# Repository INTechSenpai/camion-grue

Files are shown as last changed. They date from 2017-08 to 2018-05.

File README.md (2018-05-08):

# Après le [moon rover](https://intechsenpai.github.io/moon-rover/), INTech Senpaï est fier de vous présenter son camion grue !

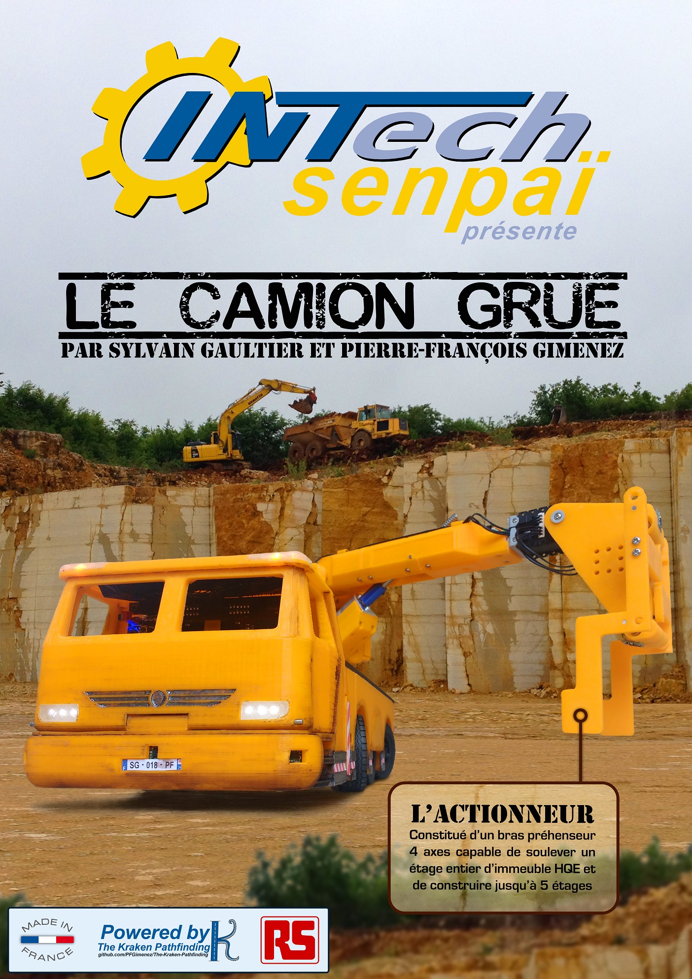
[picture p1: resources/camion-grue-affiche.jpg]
Affiche robot


## INTech Senpaï

INTech Senpaï participe pour la troisième fois à la Coupe de France de Robotique. Après le succès du robot sumo et du moon rover, qui a fini 29e à la coupe 2017, nous revenons en force avec le camion grue.

## Un modèle réduit unique

Notre camion grue est un modèle réduit à l'échelle 1:16 des immenses engins qui ont bercé notre enfance. À taille réelle, il mesurerait 3×7m ! Son design avec ses six roues (dont quatre directrices et motrices), ses feux de recul, de stop, de nuit, ses clignotants, ses gyrophare, sa grue est unique : il a été entièrement conçu par notre équipe.

## Un engin de chantier autonome

Notre camion grue utilise le système Kraken de déplacement autonome, fruit de plus de trois ans de R&D d'un doctorant en intelligence artificielle. Contrairement aux voitures autonomes qui suivent simplement une route, les engins de chantier évoluent dans un environnement encombré et changeant ; trouver un chemin implique un grand nombre de manœuvres qui peuvent être difficiles à trouver, même pour un humain. C'est ce que réalise le système Kraken, qui permet au camion grue de se déplacer avec aisance sur la table de jeu qui représente assez bien ce type d'environnement.

Le système Kraken est un logiciel libre et en [libre accès](https://github.com/PFGimenez/The-Kraken-Pathfinding).

## Un concurrent à la Coupe de France

Enfin, le camion grue est également un compétiteur de la Coupe. Sa grue terminée par une pince lui permet de manipuler des cubes et de les empiler.

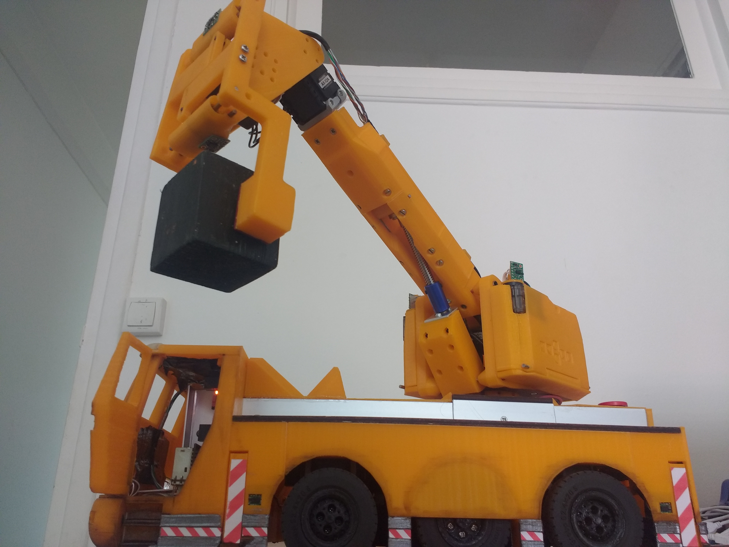
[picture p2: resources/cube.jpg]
Prise d'un cube


## Hardware

Le camion grue est équipé de quatre unités de calcul : trois Teensy pour le contrôle bas niveau et une Raspberry Pi 3+ pour Kraken. Avec ses treize capteurs _time of flight_ dont deux rotatifs, il voit tout son environnement.

On peut voir très bien un capteur _time of flight_ au centre de l'image suivante :

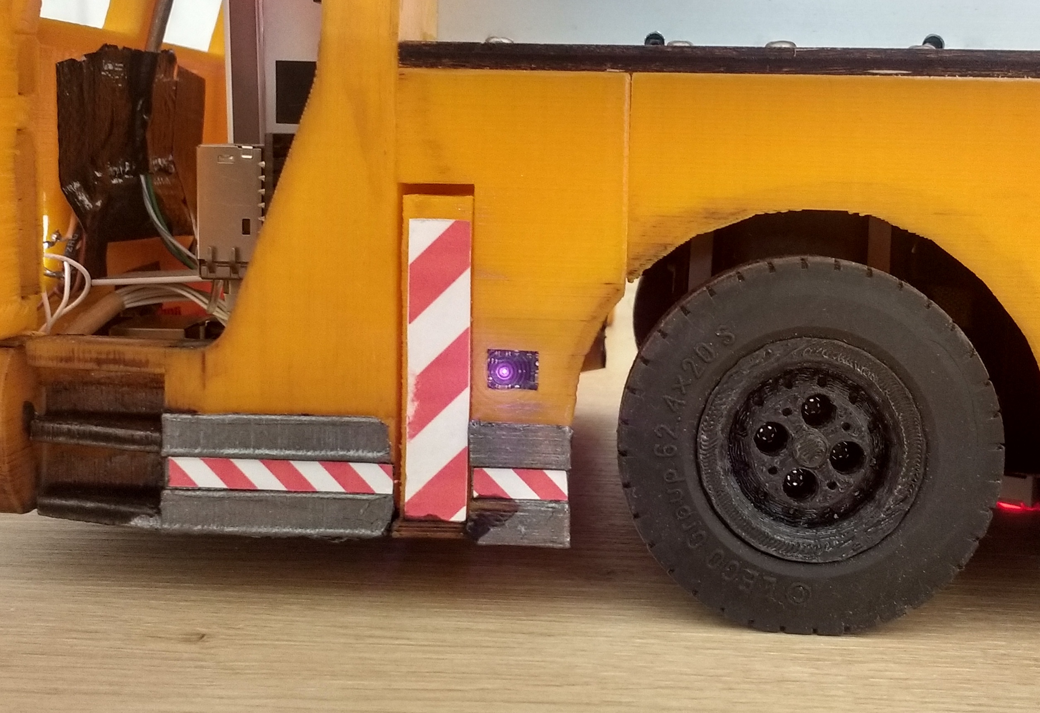
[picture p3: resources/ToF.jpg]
Capteurs ToF


Le camion grue peut facilement être ouvert afin d'accéder à son électronique.

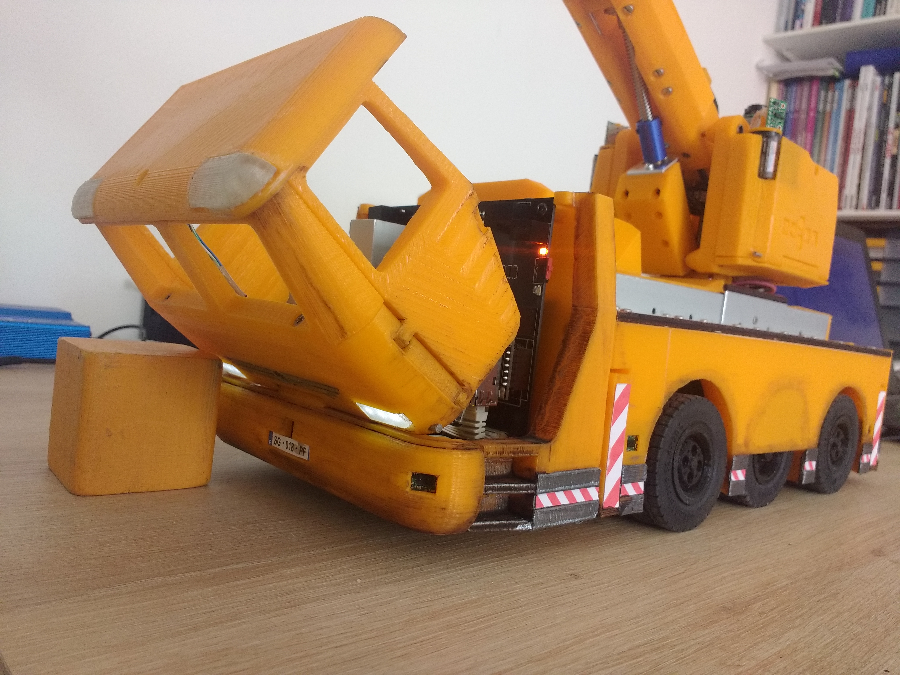
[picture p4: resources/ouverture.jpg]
Mécanisme d'ouverture


Voici une partie de l'électronique du camion. On y voit les radiateurs des ponts en H (au centre), ainsi que deux Teensy (en bas à gauche) et la Raspberry Pi (en bas). L'autre partie de l'électronique se trouve dans la grue.

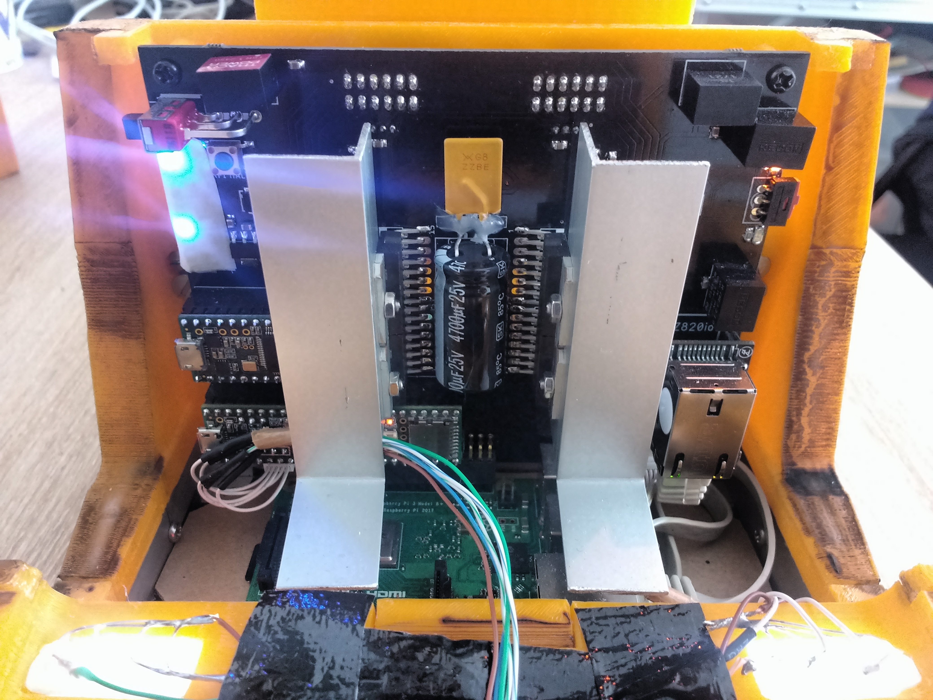
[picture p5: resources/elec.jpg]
Électronique


## L'équipe

[Sylvain Gaultier](https://github.com/sylvaing19) est le fondateur d'INTech Senpaï, il s'occupe de la conception et de la réalisation de la mécanique et de l'électronique du camion grue. Il a également programmé les trois Teensy.

[Pierre-François Gimenez](https://github.com/PFGimenez), doctorant en intelligence artificielle, a été recruté par Sylvain pour son projet de développement d'un camion grue autonome. Il est le concepteur et le programmeur du système Kraken.

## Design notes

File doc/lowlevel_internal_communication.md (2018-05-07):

# Low level: internal communication protocol

## Frame structure

| Header | Instruction | Length |  Payload  | Checksum |
|---|---|---|---|---|
| 0xFFFF | uint8_t | uint8_t| uint8_t[] |  uint8_t |
0        2             3        4          5+N        6+N    Bytes

* Length: number of bytes in the payload

## Instruction set and associated payloads

### [0x00] Sensors board report
uint8_t[9] = [front, front_left, front_right, side_front_left, side_front_right, side_back_left, side_back_right, back_left, back_right]
Values:
[4, MAX_INT]: Distance to the obstacle (mm)
3: No obstacle in front of the sensor
2: obstacle too close to measure (you can consider the distance being the minimum applicable, but not use it for repositionning)
1: Value was not updated yet (use last value instead)
0: Sensor is not working

### [0x01] Set LED lightning mode
uint8_t[1]
Values:
value & b00000001: left_turn_signal
value & b00000010: right_turn_signal
value & b00000100: flashing_lights
value & b00001000: stop_light
value & b00010000: reverse_light
value & b00100000: night_lights_low
value & b01000000: night_lights_high
value & b10000000: alarm_signal

### [0x02] Actuators board move ACK
uint8_t[0]
Indique que "isMoving" vient de passer à "true"

### [0x03] Actuators board report
uint8_t[38]
(bool)moving
(int)status
(bool)cube_in_plier
(int)tof_g
(int)tof_d
(float)angle_t_g
(float)angle_t_d
(float)angle_h_grue
(float)angle_v_grue
(float)angle_head_grue_local
(float)pos_pince_grue

### [0x04] Go to home position
uint8_t[4]
(float) deploy side (-1; 0; +1)
Retour à la position initiale du bras (avec pince entre-ouverte)

### [0x05] Take cube using sensor
uint8_t[4]
(float) angle (h) de prise (approx)

### [0x06] Take cube at fixed position
uint8_t[4]
(float) angle (h) de prise (exact)

### [0x07] Store cube inside robot
uint8_t[0]

### [0x08] Store cube on top
uint8_t[4]
(float) deploy side (-1; 0; +1)

### [0x09] Take cube from storage
uint8_t[4]
(float) deploy side (-1; 0; +1)

### [0x0A] Put cube on pile using sensor 
uint8_t[8]
(float) angle (h) de dépose (approx)
(int)floor (0=sur le sol; étage max: 4)

### [0x0B] Put cube on pile at fixed position
uint8_t[8]
(float) angle (h) de dépose (exact)
(int)floor (0=sur le sol; étage max: 4)

### [0x0C] Put arm at given position
uint8_t[16]
(float)angle_h_grue
(float)angle_v_grue
(float)angle_head_grue_local
(float)pos_pince_grue

### [0x0D] Set sensors angles
uint8_t[8]
(float)angle_t_g
(float)angle_t_d

### [0x0E] Set displayed score
uint8_t[4]
(int)score

### [0x0F] Stop arm
uint8_t[0]

### [0x10] Push button
uint8_t[8]
(float)angleV
(int) deploy side (-1; 0; +1)

### [0x11] Push bee
uint8_t[4]
(float)angleH

### [0x12] Take cube from human
uint8_t[4]
(float) deploy side (-1; 0; +1)

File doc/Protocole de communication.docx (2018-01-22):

# Protocole de communication du microcontrôleur – Eurobotruck 2018

# 1. Généralités

La communication avec le microcontrôleur responsable du contrôle du robot se fait par l’intermédiaire d’une liaison Ethernet sur laquelle est utilisé le protocole TCP/IP.

Le microcontrôleur agit comme un serveur, il peut accepter jusqu’à 4 connexions simultanées.

Un serveur identique, utilisant le même protocole et permettant d’effectuer les mêmes actions écoute également sur le port série RS232 du microcontrôleur. Aucun mécanisme de contrôle d’intégrité de l’information, de correction d’erreurs, ni d’acquittement n’est mis en place dans le protocole que nous définissons ici. La liaison série étant un support n’offrant aucune garantie de ce type, cette dernière présente un moins bon niveau de fiabilité et n’est à utiliser que si la liaison Ethernet est défaillante.

# 2. La trame

La communication entre le client et le serveur est asynchrone et se compose d’une succession de trames, formatées comme suit :

0xFF | ID | Length | Data 0 | … | Data n

Une case = un octet

0xFF : identificateur de début de trame. Simplement un octet contenant la valeur 0xFF.

ID [0x00 – 0xFF] : identifiant de trame. Octet indiquant quelle commande doit être effectuée par le microcontrôleur, ou à l’inverse quelle commande vient d’être effectuée par le microcontrôleur.

Length [0x00 – 0xFE] : taille du champ Data, en nombre d’octets. La taille totale de la trame vaut donc Length + 3. Le champ Data peut contenir, au maximum, 254 octets.

Data : ensemble d’octets contenants les informations nécessaires à l’exécution de la commande. La signification de ces octets est spécifiée plus loin, pour chaque commande.

Cas particulier : la trame d’information

La trame d’information est une trame contenant une chaine de caractères destinée à être lue par un opérateur humain. Elle sera ignorée par le serveur si il en reçois une. Elle suit le même schéma que la trame normale, à deux détails près : Length vaut 0xFF (255) et il n’y a pas de limite de taille pour la trame (la fin de la trame est donnée par le caractère de fin de chaine).

0xFF | ID | 0xFF | Char 0 | … | Char n | End of string

ID [0x00 – 0x1F] : il correspond nécessairement à celui d’un canal de données, et jamais à celui d’un ordre (voir chapitre suivant pour la définition de ces notions).

Char : succession de caractères ASCII destinés à être affichés, il s’agit du code ASCII NON étendu, ce qui interdit l’usage de caractères accentués.

Les caractères autorisés sont : \0 \t \n \r (space) ! “ # $ % & ‘ ( ) * + , - . / 0123456789 : ; < = > ? @ ABCDEFGHIJKLMNOPQRSTUVWXYZ [ \ ] ^ _ ` abcdefghijklmnopqrstuvwxyz { | } ~

Les valeurs décimales correspondantes sont : 0 ; 9 ; 10 ; 13 ; 32–126

End of string [0x00] : caractère ASCII « fin de chaine ». Octet valant zéro.

# 3. Les commandes

L’espace des 256 commandes adressables est divisé en 3 parties :

Plage d’ID | Catégorie
0 – 31 | Inscription aux canaux de données
32 – 127 | Ordres à exécution longue
128 – 255 | Ordres immédiats

## 3.1. Inscription aux canaux de données

Les ordres permettent à un client de spécifier au serveur qu’il souhaite, ou non, recevoir par la suite les informations concernant un certain canal de données. Si le client souscrit à un canal de données, il recevra des trames ayant pour ID le numéro du canal de données et contenant des informations donc le format est spécifié plus bas.

Structure de la trame d’inscription/désinscription :

0xFF | ID du canal | 0x01 | Inscription

ID du canal : valeur entre 0x00 (0) et 0x1F (31) désignant l’un des canaux de données (listés plus loin).

Inscription : 0x00 pour se désinscrire. 0x01 pour s’inscrire.

Aucune réponse ne sera envoyée par le serveur à la suite de cette commande.

Liste des canaux

Identifiant | Désignation | Format des données envoyées sur ce canal
0x00 | ODO_AND_SENSORS | (à déterminer)
0x01
0x02
0x03
0x04
0x05
0x06
…
0x1F

## 3.2. Ordres à exécution longue

On regroupe ici toutes les commandes dont la réalisation nécessite un temps « long », ce qui correspond, en pratique, à tout ce qui nécessite plus d’une milliseconde. On y trouve donc notamment les commandes mettant en œuvre des composants mécaniques.

L’exécution de l’ordre long commence à la réception de la trame de commande et se termine au bout d’un temps à priori inconnu. Une trame sera envoyée par le serveur à la fin de l’exécution de l’ordre long afin d’en notifier le client. Cette trame utilise l’identifiant de la commande et peut contenir, au besoin, des informations relatives à la qualité d’exécution de la commande. Il est interdit d’exécuter un ordre long si un autre ordre long utilisant le même identifiant (i.e. : le même ordre) est encore en cours d’exécution.

Liste des ordres longs

Identifiant | Description | Format des données de la commande | Format de données de la réponse
0x20 | FOLLOW_TRAJECTORY | None | [ARRIVED:0x00, EXT_BLOCKED:0x01, INT_BLOCKED:0x02, NO_MORE_POINTS:0x03, STOP_REQUIRED:0x04, FAR_AWAY:0x05]END_MOVE_STATUS(8) TRAJECTORY_INDEX(8)
0x21 | STOP | None | None
0x22 | WAIT_FOR_JUMPER | None | None
0x23 | START_MATCH_CHRONO
0x24 | RUN_FOR_REMOTE | None | None
0x25
0x26
…
0x7F

## 3.3. Ordres immédiats

On regroupe ici les commandes pouvant être exécutées en un temps très court devant les temps de transmission, typiquement toujours inférieur à une milliseconde. On y trouve principalement des commandes permettant de lire ou de modifier des variables d’état du système.

L’exécution d’un ordre immédiat se fait dès la réception de la trame associée, et peut faire, ou non, l’objet d’une réponse à l’aide d’une trame portant le même identifiant.

Liste des ordres immédiats

Identifiant | Description | Format des données de la commande | Format des données de la réponse
0x80 | PING | None | 0x00 (8)
0x81 | GET_COLOR | None | [ORANGE 0x00, VERT 0x01, INCONNU 0x02] (8)
0x82 | EDIT_POSITION | XYO(40) | None
0x83 | SET_POSITION | XYO(40) | None
0x84 | ADD_TRAJECTORY_POINTS | (À déterminer) | None
0x85 | SET_CURVATURE_FOR_REMOVE | CURVATURE(16) | None
0x86 | SET_SPEED_FOR_REMOTE | SIGNED_SPEED(16) | None
…
0xFF

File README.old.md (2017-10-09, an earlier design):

# Eurobotruck

Eurobotruck est le successeur du moon-rover.

TODO list :

## HL

- améliorer Kraken (objectif : 500 ms max)
- outils de debug
- tourelles
- préparer des démos à l'avance
- autocomplétion de tests + zsh + boot rapide sur linux
- outil de debug de trajectoire courbe (créer facilement des trajectoires)
- télécommande HL

## LL

- outils de debug
- tourelles
- communication par socket TCP/IP (serveur)

## Hardware

- tourelles de visée ToF longue portée (HL donne la position, LL gère la tourelle qui pointe)
- mettre des boutons pour actionneurs sur la méca

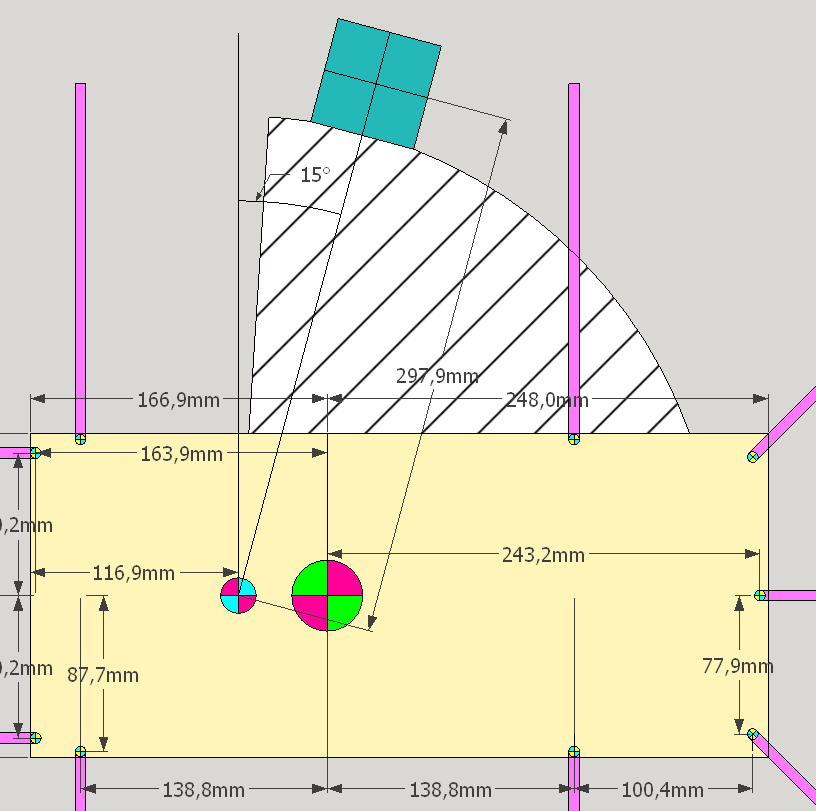
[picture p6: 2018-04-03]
doc/Position-prise-cube-detail.png

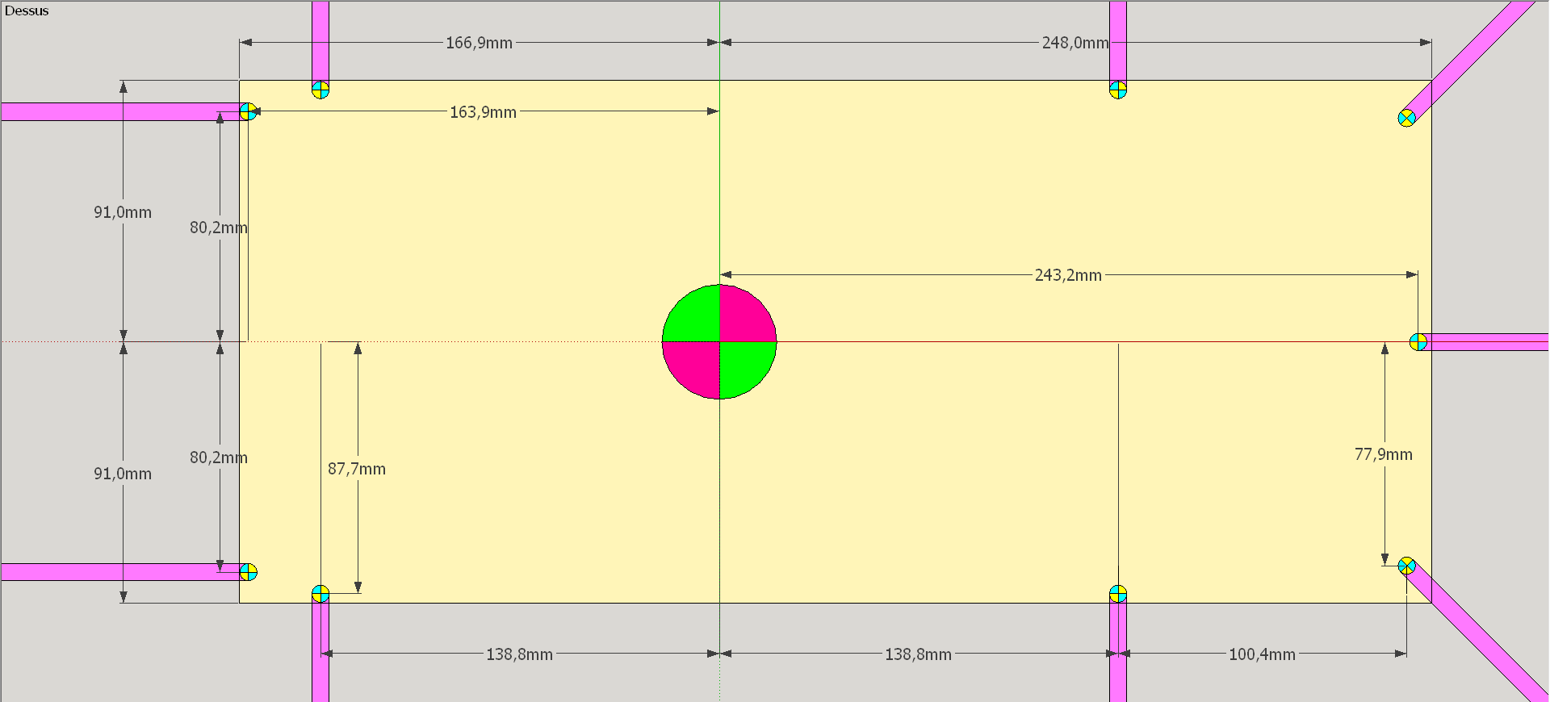
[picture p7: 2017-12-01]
doc/plan_capteurs.png

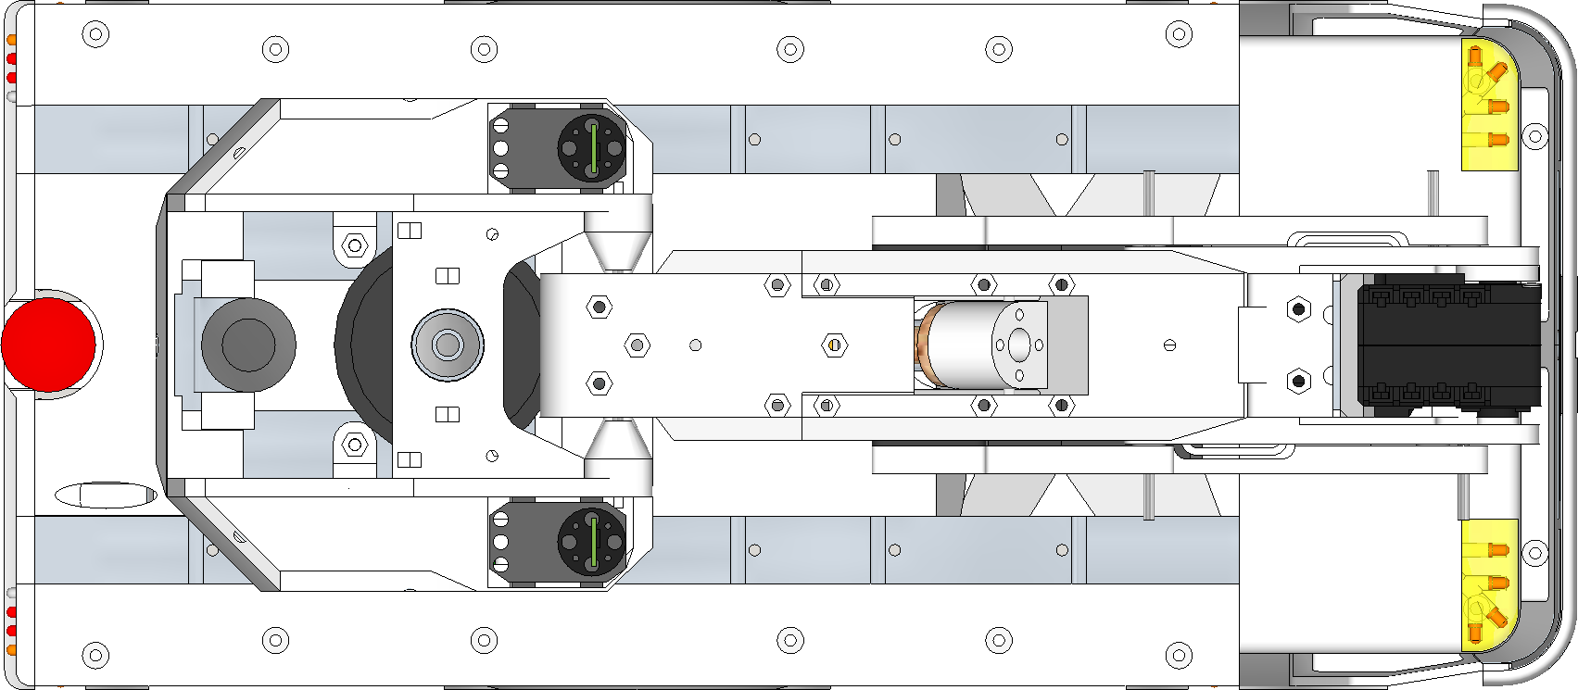
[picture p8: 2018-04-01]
high_level/src/main/resources/camion.png

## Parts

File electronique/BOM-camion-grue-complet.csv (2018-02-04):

Qty | Value | Device | Package | Parts | Description | RS
8 |  | BC817-16-NPN-SOT23-BEC | SOT23-BEC | T2, T4, T5, T6, T7, T8, T9, T10 | NPN Transistror
16 |  | BC817-16-NPN-SOT23-BEC | SOT23-BEC | T1, T3, T11, T12, T13, T14, T15, T16, T17, T18, T19, T20, T21, T22, T23, T24 | NPN Transistror | 781-4272
1 |  | PINHD-1X3 | 1X03 | USB_BACKUP_DEBUG | PIN HEADER
7 |  | PINHD-1X6 | 1X06 | DEBUG_UART, MOT_AR_D, MOT_AR_G, MOT_AV_D, MOT_AV_G, MOT_H, MOT_V | PIN HEADER
1 |  | PINHD-2X20/90 | 2X20/90 | RASPPBERRY_PI | PIN HEADER
1 |  | SWITCH_LPV-1 | SWITCH_LPV-1 | S1 | TOGGLE SWITCH | 734-7306
36 | 0 | R-EU_R0805 | R0805 | R15, R17, R20, R22, R24, R26, R28, R30, R32, R34, R40, R42, R46, R47, R48, R49, R50, R51, R52, R53, R54, R55, R56, R57, R58, R63, R64, R65, R70, R71, R72, R73, R74, R75, R76, R77 | RESISTOR, European symbol
10 | 100nF | C-EUC0805 | C0805 | H-BRIDGE1:C1, H-BRIDGE1:C2, H-BRIDGE_AR_D:C1, H-BRIDGE_AR_D:C2, H-BRIDGE_AR_G:C1, H-BRIDGE_AR_G:C2, H-BRIDGE_AV_D:C1, H-BRIDGE_AV_D:C2, H-BRIDGE_AV_G:C1, H-BRIDGE_AV_G:C2 | CAPACITOR, European symbol
30 | 10k | R-EU_R0805 | R0805 | H-BRIDGE1:R1, H-BRIDGE1:R2, H-BRIDGE1:R3, H-BRIDGE1:R4, H-BRIDGE1:R5, H-BRIDGE1:R6, H-BRIDGE_AR_D:R1, H-BRIDGE_AR_D:R2, H-BRIDGE_AR_D:R3, H-BRIDGE_AR_G:R1, H-BRIDGE_AR_G:R2, H-BRIDGE_AR_G:R3, H-BRIDGE_AV_D:R1, H-BRIDGE_AV_D:R2, H-BRIDGE_AV_D:R3, H-BRIDGE_AV_G:R1, H-BRIDGE_AV_G:R2, H-BRIDGE_AV_G:R3, MULTI-BUTTON-1:R3, MULTI-BUTTON-2:R3, R2, R3, R6, R7, R8, R9, R35, R36, R37, R38 | RESISTOR, European symbol
10 | 10µF | C-EUC0805 | C0805 | C1, C2, C3, C4, C9, C14, C15, C18, C19, C20 | CAPACITOR, European symbol
2 | 1k | R-EU_R0805 | R0805 | R44, R82 | RESISTOR, European symbol
9 | 1µF | C-EUC0805 | C0805 | C5, C6, C7, C8, C12, C13, C17, MULTI-BUTTON-1:C1, MULTI-BUTTON-2:C1 | CAPACITOR, European symbol
1 | 220 | R-EU_R0805 | R0805 | R43 | RESISTOR, European symbol
1 | 22k | R-EU_R0805 | R0805 | R11 | RESISTOR, European symbol
2 | 22µF | C-EUC0805 | C0805 | C11, C16 | CAPACITOR, European symbol
24 | 270 | R-EU_R0805 | R0805 | R16, R18, R19, R21, R23, R25, R27, R29, R31, R33, R39, R41, R59, R60, R61, R62, R66, R67, R68, R69, R78, R79, R80, R81 | RESISTOR, European symbol
2 | 2k2 | R-EU_R0805 | R0805 | MULTI-BUTTON-1:R2, MULTI-BUTTON-2:R2 | RESISTOR, European symbol
5 | 330 | R-EU_R0805 | R0805 | R4, R5, R10, R13, R14 | RESISTOR, European symbol
2 | 470 | R-EU_R0805 | R0805 | R1, R45 | RESISTOR, European symbol
1 | 4700µF | CPOL-EUTT5D11L | TT5D11L | C10 | POLARIZED CAPACITOR, European symbol
2 | 4k7 | R-EU_R0805 | R0805 | MULTI-BUTTON-1:R1, MULTI-BUTTON-2:R1 | RESISTOR, European symbol
1 | 6k8 | R-EU_R0805 | R0805 | R12 | RESISTOR, European symbol
4 | BSS138 | BSS123 | SOT23 | Q1, Q2, Q3, Q4 | N-CHANNEL MOS FET
1 | DC-DC-CONVERTER | DC-DC-CONVERTER | DC-DC-CONVERTER | DC-DC-6V |  | 715-8575
1 | DIODE_S15P45 | DIODE_S15P45 | TO-277A | D1
3 | DYNAMIXEL-1X03AX | DYNAMIXEL-1X03AX | DYNAMIXEL_AX_1X03 | AX12_D, AX12_G, AX12_G1
4 | DYNAMIXEL-1X03XL | DYNAMIXEL-1X03XL | DYNAMIXEL_XL_1X03 | XL320_D, XL320_G, XL320_G1, XL320_G2
1 | JST-03 | JST-03 | GH-03-V | JUMPER
4 | JST-04GH-V | JST-04GH-V | GH-04-V | ENCODEUR_DROIT, ENCODEUR_GAUCHE, GYRO, LIPO1
3 | JST-05 | JST-05 | GH-05-V | DEL_GYRO, TOF_LP_D_AND_DISPLAY, TOF_LP_G
1 | JST-06 | JST-06 | GH-06-V | TOF_PINCE
3 | JST-10 | JST-10 | GH-10-V | GRUE, GRUE1, PHARES_ET_TOF_AV
2 | JST-12 | JST-12 | GH-12-V | ARRET_URGENCE, LIPO
1 | JST-15 | JST-15 | GH-15-V | DELS_ET_TOF_AR
5 | L298 | L298 | MULTIWATT-15 | H-BRIDGE1:IC1, H-BRIDGE_AR_D:IC1, H-BRIDGE_AR_G:IC1, H-BRIDGE_AV_D:IC1, H-BRIDGE_AV_G:IC1 | DUAL FULL-BRIDGE DRIVER
1 | MF-LSMF300 | MF-LSMF300 | MF-LSMF300 | F1 | PolySwitch (TM) Resettable Device | 817-1652
1 | MF-MSMF110 | MF-MSMF110 | MF-MSMF110 | F2 |  | 647-8207
6 | PUSH-BUTTON | PUSH-BUTTON | PUSH-BUTTON | MULTI-BUTTON-1:U1, MULTI-BUTTON-1:U2, MULTI-BUTTON-1:U3, MULTI-BUTTON-2:U1, MULTI-BUTTON-2:U2, MULTI-BUTTON-2:U3 |  | 479-1491
2 | PUSH-BUTTON | PUSH-BUTTON | PUSH-BUTTON | U$2, U$4 |  | 479-1491
4 | R-78C3.3-1.0 | R-78C3.3-1.0 | SIP3 | DC1, DC2, DC5, DC7 | INNOLINE DC/DC-Converter 1.0 AMP SIP3 Single Output
2 | R-78C5.0-1.0 | R-78C5.0-1.0 | SIP3 | DC3, DC6 | INNOLINE DC/DC-Converter 1.0 AMP SIP3 Single Output
1 | R-78C9.0-1.0 | R-78C9.0-1.0 | SIP3 | DC4 | INNOLINE DC/DC-Converter 1.0 AMP SIP3 Single Output
2 | REG1117 | REG1117 | SOT223 | IC1, IC3 | 800mA and 1A Low Dropout (LDO) Positive Regulator | 885-5432
1 | RGEF800 | RGEF800 | 5MM | P1 |  | 517-6966
1 | RPI-ZERO | RPI-ZERO | RASPBERRYPI_BASTELSTUBE_V13_RASPI_BOARD_B+_FULL | RPI
25 | S1M | S1M | SMA | D2, H-BRIDGE1:D1, H-BRIDGE1:D2, H-BRIDGE1:D3, H-BRIDGE1:D4, H-BRIDGE1:D5, H-BRIDGE1:D6, H-BRIDGE1:D7, H-BRIDGE1:D8, H-BRIDGE_AR_D:D1, H-BRIDGE_AR_D:D2, H-BRIDGE_AR_D:D3, H-BRIDGE_AR_D:D4, H-BRIDGE_AR_G:D1, H-BRIDGE_AR_G:D2, H-BRIDGE_AR_G:D3, H-BRIDGE_AR_G:D4, H-BRIDGE_AV_D:D1, H-BRIDGE_AV_D:D2, H-BRIDGE_AV_D:D3, H-BRIDGE_AV_D:D4, H-BRIDGE_AV_G:D1, H-BRIDGE_AV_G:D2, H-BRIDGE_AV_G:D3, H-BRIDGE_AV_G:D4 |  | 872-2874
1 | TEENSY_3.1-3.2_DIL | TEENSY_3.1-3.2_DIL | TEENSY_3.0-3.2&LC_DIL | U2 | Teensy 3.1 or 3.2 in a DIL Layout.
1 | TEENSY_3.1-3.2_DIL+4 | TEENSY_3.1-3.2_DIL+4 | TEENSY_3.0-3.2&LC_DIL+4 | U$1 | Teensy 3.1 and 3.2 in a DIL package with the inner 4 pins
1 | TEENSY_3.5_DIL+USB | TEENSY_3.5_DIL+USB | TEENSY_3.5_DIL+USB | U1
2 | TL36PO | TL36PO | TL3XPO | S2, S3 | TINY SWITCH ON - ON | 913-9069
1 | WIZ820IO | WIZ820IO | WIZ820 | U$3
25 | bleu | LED5MM | LED5MM | LED36, LED58, LED59, LED60, LED61, LED62, LED63, LED64, LED98, LED102, LED124, LED125, LED126, LED127, LED128, LED129, LED130, LED134, LED156, LED157, LED158, LED159, LED160, LED161, LED162 | LED
2 | blue | LEDSMT1206 | 1206 | LED1, LED5 | LED
1 | green | LEDSMT1206 | 1206 | LED2 | LED
24 | jaune | LED5MM | LED5MM | LED34, LED51, LED52, LED53, LED54, LED55, LED56, LED57, LED100, LED117, LED118, LED119, LED120, LED121, LED122, LED123, LED132, LED149, LED150, LED151, LED152, LED153, LED154, LED155 | LED
24 | orange | LED5MM | LED5MM | LED33, LED37, LED38, LED39, LED40, LED41, LED42, LED43, LED99, LED103, LED104, LED105, LED106, LED107, LED108, LED109, LED131, LED135, LED136, LED137, LED138, LED139, LED140, LED141 | LED
1 | orange | LEDSMT1206 | 1206 | LED3 | LED
2 | red | LEDSMT1206 | 1206 | LED4, LED6 | LED
25 | vert | LED5MM | LED5MM | LED35, LED44, LED45, LED46, LED47, LED48, LED49, LED50, LED97, LED101, LED110, LED111, LED112, LED113, LED114, LED115, LED116, LED133, LED142, LED143, LED144, LED145, LED146, LED147, LED148 | LED

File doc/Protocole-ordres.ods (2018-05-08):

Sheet: Info_générales
Types primitifs | Abbréviation | Nombre d’octets | Nombre de bits | Structure | Abbréviation | Composition
Float | float | 4 | 32 | TRAJECTORY_POINT | PT | POSITION_XYO (XYO) COURBURE (float) SPEED (float) STOP POINT (bool) END_OF_TRAJECTORY (bool)
Signed int | int32 | 4 | 32 | XYO | XYO | POSITION_X (int32) POSITION_Y (int32) ORIENTATION (float)
Booléen | bool | 1 | 8 | SENSORS | SSR | ToF_AVANT (int32) ToF_COIN_AVANT_GAUCHE (int32) ToF_COIN_AVANT_DROIT (int32) ToF_LATERAL_AVANT_GAUCHE (int32) ToF_LATERAL_AVANT_DROIT (int32) ToF_LATERAL_ARRIERE_GAUCHE (int32) ToF_LATERAL_ARRIERE_DROIT (int32) ToF_ARRIERE_GAUCHE (int32) ToF_ARRIERE_DROITE (int32) TOURELLE_GAUCHE (int32) TOURELLE_DROITE (int32) ANGLE_TOURELLE_GAUCHE (float) ANGLE_TOURELLE_DROITE (float) ANGLE_GRUE (float)
Enum | enum | 1 | 8
Enum | Nom (valeur) | Description
ETAT_MOUVEMENT | MOVE_OK (0x00) | Le robot est arrivé à destination (qui est un stop point), il n’a plus aucun point dans sa trajectoire
 | EMERGENCY_BREAK (0x01) | Le robot a dû s’arrêter suite à une demande explicite du HL (STOP)
 | EXT_BLOCKED (0x02) | Le robot a dû s’arrêter à cause d’un blocage externe
 | INT_BLOCKED (0x04) | Le robot a dû s’arrêter à cause d’un blocage interne
 | FAR_AWAY (0x08) | Le robot a dû s’arrêter car son écart à la trajectoire prévue est trop grand
 | EMPTY_TRAJ (0x10) | Le robot n’a plus de points à parcourir. Soit la trajectoire était déjà vide, soit son dernier point n’était pas un « end of trajectory »
COULEUR_ROBOT | ORANGE (0x00) | Le robot part du côté orange
 | VERT (0x01) | Le robot part du côté vert
 | UNKNOWN (0x02) | Le robot ne sait pas de quelle couleur il est
CODE_RETOUR | SUCCESS (0x00) | La commande a fonctionné nominalement
 | FAILURE (0x01) | La commande a rencontré un problème
MOTION_CONTROL_LEVEL | NONE (0x00) | Aucun moteur ne peut bouger
 | PWM_CONTROLLED (0x01) | Les PWM sont envoyés auw moteurs
 | SPEED_CONTROLED (0x02) | Les PWM sont calculés par l'asservissement en vitesse
 | TRANSLATION_CONTROLLED (0x03) | La vitesse consigne est calculée par l'asservissement en translation
 | TRAJECTORY_CONTROLLED (0x04) | La consigne en courbure et la distance à parcourir sont contrôlées par l'asservissement sur trajectoire
MOTOR_TO_TEST | NONE (0x00) | Moteur auquel s'appliquent les ordres SET_PWM, SPEED_KP, etc…
 | FRONT_LEFT (0x01)
 | FRONT_RIGHT (0x02)
 | BACK_LEFT (0x03)
 | BACK_RIGHT (0x04)
CODE_RETOUR_ACTIONNEUR | OK (0x00) | Tout va bien
 | H-MOTOR_BLOCKED (0x01) | Moteur horizontal bloqué physiquement
 | V-MOTOR_BLOCKED (0x02) | Moteur vertical bloqué physiquement
 | AX12_BLOCKED (0x04) | Un des AX12 a retourné une erreur "OVERLOAD" ou "OVERHEAT"
 | AX12_ERR (0x08) | Un des AX12 a retourné une autre erreur
 | MANUAL_STOP (0x10) | L'arrêt a été explicitement demandé durant l'exécution
 | UNREACHABLE (0x20) | L'angle donné comme consigne n'est pas ateignable
 | SENSOR_ERR (0x40) | Un des capteurs est HS
 | NO_DETECTION (0x80) | Le cube n'a pas été vu lors du passage, le mouvement a été tenté à la position par défaut
 | COMMUNICATION_ERR (0x100) | La communication interne du LL est défaillante
 | CUBE_MISSED (0x200) | Le cube n'est pas détecté dans la pince après une opération de préhension
 | MOVE_TIMED_OUT (0x400) | Le mouvement ne s'est pas terminé pendant le temps imparti
Nom | Unité | Repère
ORIENTATION | rad | Repère trigo classique = celui d’INTech
POSITION_X | mm | De -1500 à 1500 (celui d’INTech)
POSITION_Y | mm | De 0 à 2000 (celui d’INTech)
COURBURE | m⁻¹ | Positif : tourne vers la gauche. Négatif : tourne vers la droite.
SPEED | mm/s | Positif : marche avant. Négatif : marche arrière.
Format des données de capteur (int32)
Valeurs réservées
0x00 | Capteur HS (débranché, brûlé, noyé, etc…)
0x01 | Pas de nouvelle mesure effectuée pour l'instant (si une valeur est nécessaire, utiliser celle donnée dans la trame précédente)
0x02 | Obstacle trop proche pour effectuer une mesure précise (si une valeur est nécessaire, utiliser le minimum qui ait du sens. Non utilisable pour un recalage dynamique sur bord de table)
0x03 | Aucun obstacle détecté, on fonçe !
Autres valeurs
0x04 -> MAX_INT32 | Distance de l'obstacle détecté, en mm

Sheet: Canaux
Nom | Identifiant | Format | Description
ODO_AND_SENSORS | 0x00 | POSITION_XYO (XYO) COURBURE (float) TRAJECTORY_INDEX (int32) IS_MOVING_FORWARD (bool) SENSORS (SSR) | Les données d’odométrie doivent être, dans la même mesure du possible, mesurées simultanément aux capteurs.
INFO | 0x01 | DEBUG ASCII TEXT
ERRORS | 0x02 | DEBUG ASCII TEXT
TRACE | 0x03 | DEBUG ASCII TEXT
SPY_ORDERS | 0x04 | DEBUG ASCII TEXT
DIRECTION | 0x05 | DEBUG ASCII TEXT
AIM_TRAJECTORY | 0x06 | DEBUG ASCII TEXT
SPEED_PID | 0x07 | DEBUG ASCII TEXT
TRANSLATION_PID | 0x08 | DEBUG ASCII TEXT
TRAJECTORY_PID | 0x09 | DEBUG ASCII TEXT
BLOCKING_MGR | 0x0A | DEBUG ASCII TEXT
STOPPING_MGR | 0x0B | DEBUG ASCII TEXT

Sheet: Ordres_longs
Nom | Identifiant | Données | Réponse | Description
FOLLOW_TRAJECTORY | 0x20 | NA | ETAT_FIN_TRAJECTOIRE (int32) | Le robot avance jusqu’à avoir parcouru tous les points de la trajectoire ou jusqu’à rencontrer un problème
STOP | 0x21 | NA | NA | Le robot doit s’arrêter dès que possible
WAIT_FOR_JUMPER | 0x22 | NA | NA | L’ordre doit s’arrêter dès que le jumper est retiré.
START_CHRONO_MATCH | 0x23 | NA | NA | L’ordre doit s’arrêter au bout de 100s.
ARM_GO_HOME | 0x24 | DEPLOY_SIDE (float) | CODE_RETOUR_ACTIONNEUR (int32) | Retour à la position "rangée", permettant les déplacements
ARM_TAKE_CUBE_S | 0x25 | ANGLE_H (float) | CODE_RETOUR_ACTIONNEUR (int32) | Prise d'un cube placé proche de l'ange donné., le capteur servira à repérer sa position exacte
ARM_TAKE_CUBE | 0x26 | ANGLE_H (float) | CODE_RETOUR_ACTIONNEUR (int32) | Prise d'un cube à la position donnée (option la plus rapide)
ARM_STORE_CUBE_INSIDE | 0x27 | NA | CODE_RETOUR_ACTIONNEUR (int32) | Dépose d'un cube dans la zone de stockage interne (présuppose qu'un cube soit pris dans la pince)
ARM_STORE_CUBE_TOP | 0x28 | DEPLOY_SIDE (float) | CODE_RETOUR_ACTIONNEUR (int32) | Placement du cube au dessus de la tête pour se déplacer tout en gardant le cube dans la pince
ARM_TAKE_FROM_STORAGE | 0x29 | DEPLOY_SIDE (float) | CODE_RETOUR_ACTIONNEUR (int32) | Prise du cube présent dans la zone de stockage
ARM_PUT_ON_PILE_S | 0x2A | ANGLE_H (float), FLOOR (int32) | CODE_RETOUR_ACTIONNEUR (int32) | Dépose le cube sur une pile, à l'angle donné, à l'étage donné, en utilisant les capteurs
ARM_PUT_ON_PILE | 0x2B | ANGLE_H (float), FLOOR (int32) | CODE_RETOUR_ACTIONNEUR (int32) | Dépose le cube sur une pile, à l'angle donné, à l'étage donné
ARM_GO_TO | 0x2C | ANGLE_H (float), ANGLE_V (float), ANGLE_HEAD (float), POS_PLIER (float) | CODE_RETOUR_ACTIONNEUR (int32) | Donne directement une consigne de positionnement au bras
ARM_STOP | 0x2D | NA | NA | Arrêt immédiat des mouvements du bras
ARM_PUSH_BUTTON | 0x2E | ANGLE_V (float), DEPLOY_SIDE (int32) | CODE_RETOUR_ACTIONNEUR (int32) | Pousse le bouton
ARM_PUSH_BEE | 0x2F | ANGLE (float) | CODE_RETOUR_ACTIONNEUR (int32) | Pousse l'abeille
ARM_TAKE_CUBE_FROM_HUMAN | 0x30 | DEPLOY_SIDE (float) | CODE_RETOUR_ACTIONNEUR (int32) | Prends un cube des mains d'un pauvre humain

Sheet: Ordres_courts
Nom | Identifiant | Données | Réponse | Description
PING | 0x80 | NA | 0x00 (int32) | Permet de savoir si le LL est présent ou non.
GET_COLOR | 0x81 | NA | COULEUR_ROBOT (enum) | Renvoie la couleur du robot
EDIT_POSITION | 0x82 | XYO | NA | Le LL doit ajouter le XYO en paramètre à son état actuel
SET_POSITION | 0x83 | XYO | NA | Le LL doit remplacer son état actuel par le XYO en paramètre
APPEND_TRAJECTORY_POINTS | 0x84 | [TRAJECTORY_POINT, … ] | CODE_RETOUR (enum) | Ajoute tous les TRAJECTORY_POINT fournis à la suite de la trajectoire courante.
EDIT_TAJECTORY_POINT | 0x85 | INDEX (int32), TRAJECTORY_POINT | CODE_RETOUR (enum) | Remplace le point d'indice INDEX par celui donné en argument
DELETE_TRAJECTORY_POINTS | 0x86 | INDEX (int32) | CODE_RETOUR (enum) | Tous les points dont l'indice est supérieur ou égal à l'indice en paramètre doivent être détruits (ils ne font plus partis de la trajectoire)
SET_SENSORS_ANGLES | 0x87 | LEFT_ANGLE (float), RIGHT_ANGLE (float) | NA | Règle l'angle des XL320 sur lesquels sont montés les capteurs longue portée
SET_SCORE | 0x88 | SCORE (int32) | NA | Règle le score affiché sur le robot
GET_ARM_POSITION | 0x89 | NA | ANGLE_H (float), ANGLE_V (float), ANGLE_HEAD (float), POS_PLIER (float) | Retourne la position du bras
 | 0x8A
 | 0x8B
 | 0x8C
 | 0x8D
 | 0x8E
 | 0x8F
DISPLAY | 0x90 | NA | NA | Affiche dans le canal INFO les constantes d'asservissement
SAVE | 0x91 | NA | NA | Sauvegarde les réglages courants dans l'EEPROM
LOAD_DEFAULTS | 0x92 | NA | NA | Rétablis les réglages par défaut à l'aide des données du code source
GET_POSITION | 0x93 | NA | XYO | Donne la position courante du robot
GET_BATTERY | 0x94 | NA | BATTERY_LEVEL (int32) | Renvoie le pourcentage de batterie restant
SET_CONTROL_LEVEL | 0x95 | MOTION_CONTROL_LEVEL (Enum) | NA | Réglage du niveau de contrôle de la position/vitesse/trajectoire
SET_MONITORED_MOTOR | 0x96 | MOTOR_TO_TEST (Enum) | NA | Sélection du moteur à régler et tester
START_MANUAL_MOVE | 0x97 | NA | NA | Démarre un mouvement, sans point de trajectoire
SET_PWM | 0x98 | PWM (int32) | NA | Règle le PWM du moteur courant
SET_MAX_SPEED | 0x99 | MAX_SPEED (float) | NA | Règle la consigne en vitesse (car si la transation n'est pas contrôlée, la consigne en vitesse est la vitesse maximale)
SET_DISTANCE_TO_DRIVE | 0x9A | DISTANCE_TO_DRIVE (float) | NA | Règle la consigne en translation
SET_CURVATURE | 0x9B | CURVATURE (float) | NA | Règle la consigne en courbure
SPEED_CONSTANTS | 0x9C | KP (float) KI (float) KD (float) | NA
TRANSLATION_CONSTANTS | 0x9D | KP (float) KD (float) | NA
TRAJECTORY_CONSTANTS | 0x9E | K1 (float) K2 (float) | NA
BLOCKING_CONSTANTS | 0x9F | SENSIBILITY (float) RESPONSE_TIME (int32) | NA
STOPPING_CONSTANTS | 0xA0 | STOPPED_SPEED (float) RESPONSE_TIME (int32) | NA
SET_MAX_ACCELERATION | 0xA1 | ACCELERATION (float) | NA
SET_MAX_DECELERATION | 0xA2 | DECELERATION (float) | NA
SET_MAX_CURVATURE | 0xA3 | CURVATURE (float) | NA

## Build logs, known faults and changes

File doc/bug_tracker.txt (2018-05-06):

# TODO

Régler détection des blocages physiques des moteurs CC grue
Ajouter ordre "pushBee"
Ajouter des paramètres à l'ordre "pushButton"

# Bug tracker

Lib XL320 à réécrire car cause hardfault

# Fixed
ArmController : initial position incorrect
Manual AX12 movement

# Known issues
Overclock on teensy 3.2 (to 96MHz) cause i2c bus to fail

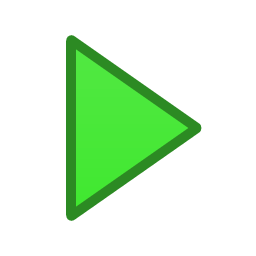
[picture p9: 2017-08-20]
debug_tools/lowlevel_interface/img/send.png

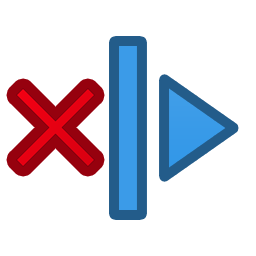
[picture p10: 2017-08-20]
debug_tools/lowlevel_interface/img/erase.png

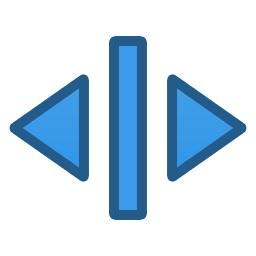
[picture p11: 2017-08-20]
debug_tools/lowlevel_interface/img/cut.png

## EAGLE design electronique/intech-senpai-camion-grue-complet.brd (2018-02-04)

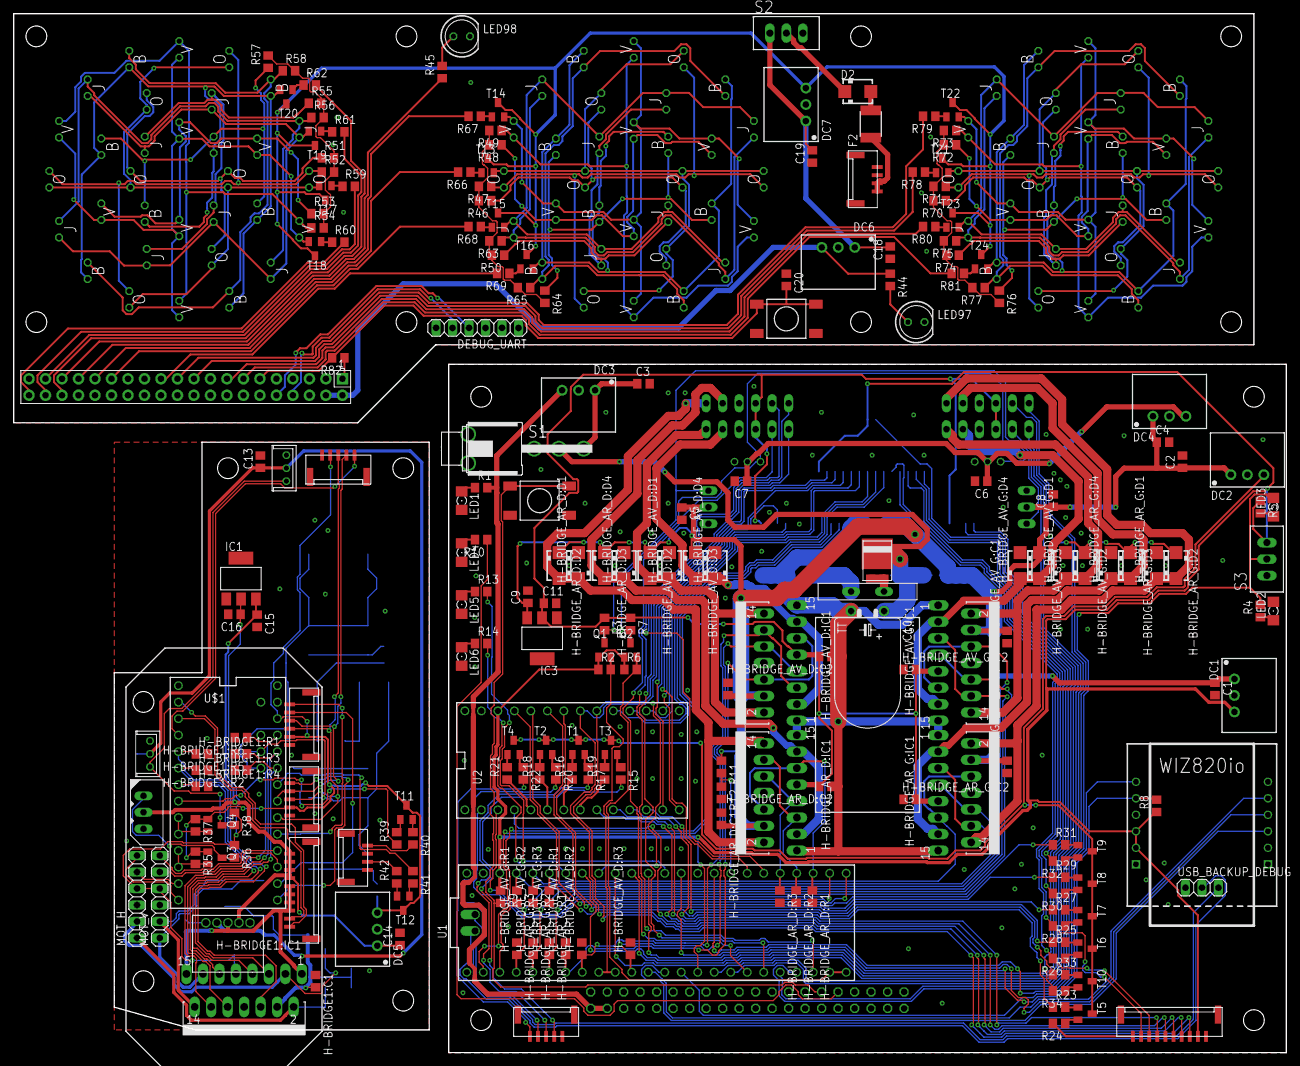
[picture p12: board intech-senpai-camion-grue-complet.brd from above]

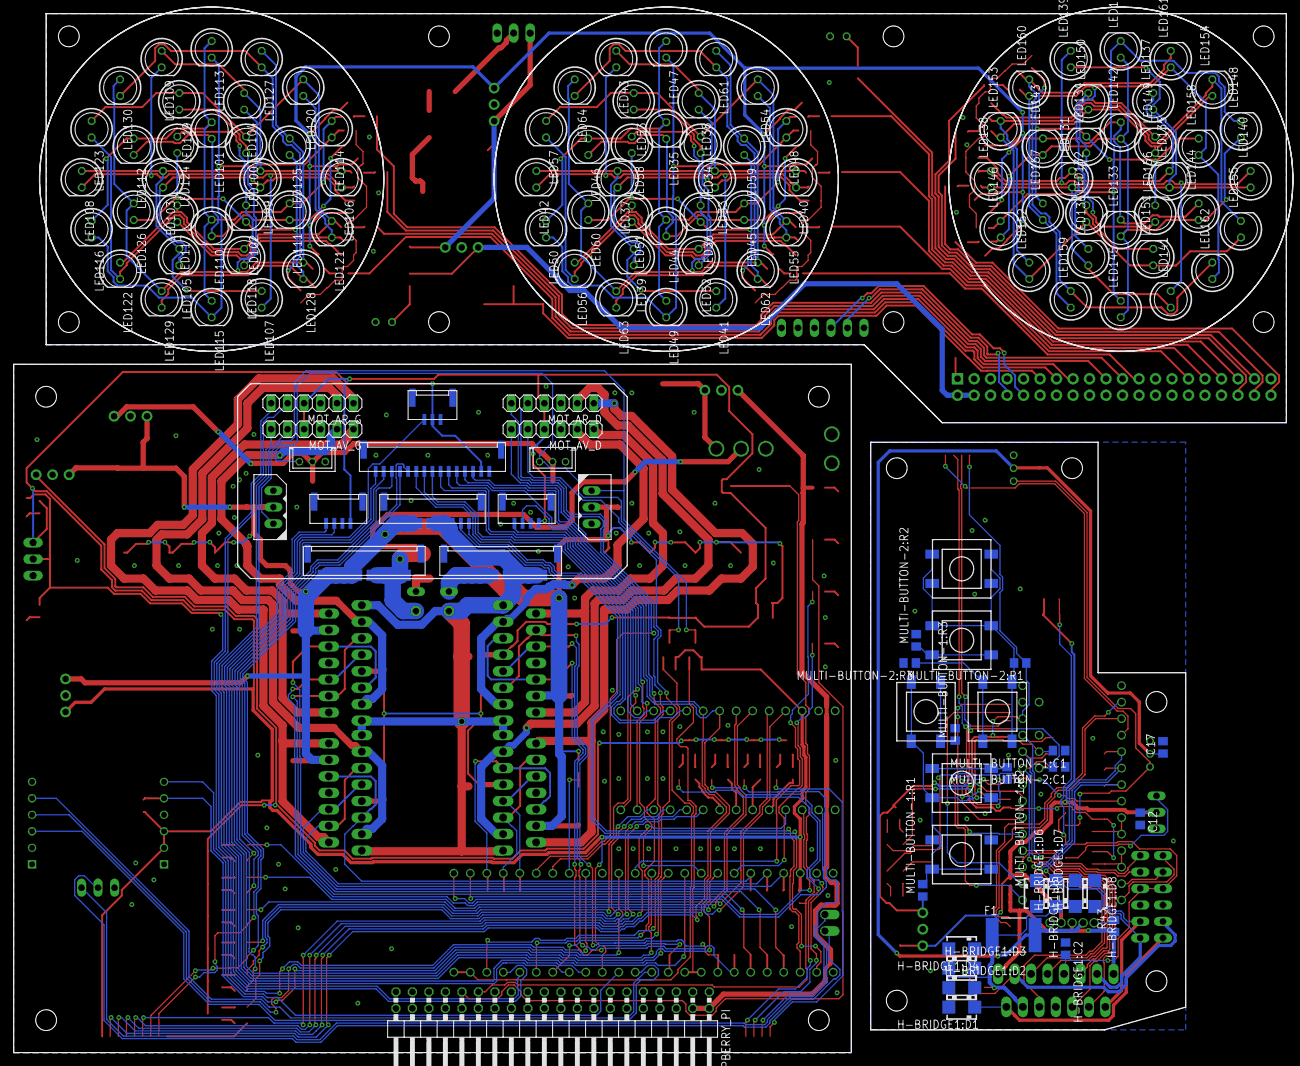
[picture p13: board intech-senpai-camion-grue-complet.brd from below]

Board: 2 copper layers, 196.0 x 160.0 mm, 361 parts (139 on the bottom side), 243 nets.

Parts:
ARRET_URGENCE: JST-12; GH-12-V
AX12_D, AX12_G, AX12_G1: DYNAMIXEL-1X03AX; DYNAMIXEL_AX_1X03
C1, C2, C3, C4, C9, C14, C15, C18, C19, C20: 10µF; C0805
C5, C6, C7, C8, C12, C13, C17: 1µF; C0805
C10: 4700µF; TT5D11L
C11, C16: 22µF; C0805
D1: DIODE_S15P45; TO-277A
D2: S1M; SMA
DC1, DC2, DC5, DC7: R-78C3.3-1.0; SIP3
DC3, DC6: R-78C5.0-1.0; SIP3
DC4: R-78C9.0-1.0; SIP3
DC-DC-6V: DC-DC-CONVERTER
DEBUG_UART: 1X06
DELS_ET_TOF_AR: JST-15; GH-15-V
DEL_GYRO: JST-05; GH-05-V
ENCODEUR_DROIT: JST-04GH-V; GH-04-V
ENCODEUR_GAUCHE: JST-04GH-V; GH-04-V
F1: MF-LSMF300
F2: MF-MSMF110
GRUE, GRUE1: JST-10; GH-10-V
GYRO: JST-04GH-V; GH-04-V
H-BRIDGE1:C1, H-BRIDGE1:C2: 100nF; C0805
H-BRIDGE1:D1, H-BRIDGE1:D2, H-BRIDGE1:D3, H-BRIDGE1:D4, H-BRIDGE1:D5, H-BRIDGE1:D6, H-BRIDGE1:D7, H-BRIDGE1:D8: S1M; SMA
H-BRIDGE1:IC1: L298; MULTIWATT-15
H-BRIDGE1:R1, H-BRIDGE1:R2, H-BRIDGE1:R3, H-BRIDGE1:R4, H-BRIDGE1:R5, H-BRIDGE1:R6: 10k; R0805
H-BRIDGE_AR_D:C1, H-BRIDGE_AR_D:C2: 100nF; C0805
H-BRIDGE_AR_D:D1, H-BRIDGE_AR_D:D2, H-BRIDGE_AR_D:D3, H-BRIDGE_AR_D:D4: S1M; SMA
H-BRIDGE_AR_D:IC1: L298; MULTIWATT-15
H-BRIDGE_AR_D:R1, H-BRIDGE_AR_D:R2, H-BRIDGE_AR_D:R3: 10k; R0805
H-BRIDGE_AR_G:C1, H-BRIDGE_AR_G:C2: 100nF; C0805
H-BRIDGE_AR_G:D1, H-BRIDGE_AR_G:D2, H-BRIDGE_AR_G:D3, H-BRIDGE_AR_G:D4: S1M; SMA
H-BRIDGE_AR_G:IC1: L298; MULTIWATT-15
H-BRIDGE_AR_G:R1, H-BRIDGE_AR_G:R2, H-BRIDGE_AR_G:R3: 10k; R0805
H-BRIDGE_AV_D:C1, H-BRIDGE_AV_D:C2: 100nF; C0805
H-BRIDGE_AV_D:D1, H-BRIDGE_AV_D:D2, H-BRIDGE_AV_D:D3, H-BRIDGE_AV_D:D4: S1M; SMA
H-BRIDGE_AV_D:IC1: L298; MULTIWATT-15
H-BRIDGE_AV_D:R1, H-BRIDGE_AV_D:R2, H-BRIDGE_AV_D:R3: 10k; R0805
H-BRIDGE_AV_G:C1, H-BRIDGE_AV_G:C2: 100nF; C0805
H-BRIDGE_AV_G:D1, H-BRIDGE_AV_G:D2, H-BRIDGE_AV_G:D3, H-BRIDGE_AV_G:D4: S1M; SMA
H-BRIDGE_AV_G:IC1: L298; MULTIWATT-15
H-BRIDGE_AV_G:R1, H-BRIDGE_AV_G:R2, H-BRIDGE_AV_G:R3: 10k; R0805
IC1, IC3: REG1117; SOT223
JUMPER: JST-03; GH-03-V
LED1, LED5: blue; 1206
LED2: green; 1206
LED3: orange; 1206
LED4, LED6: red; 1206
LED33, LED37, LED38, LED39, LED40, LED41, LED42, LED43, LED99, LED103, LED104, LED105, LED106, LED107, LED108, LED109, LED131, LED135, LED136, LED137, LED138, LED139, LED140, LED141: orange; LED5MM
LED34, LED51, LED52, LED53, LED54, LED55, LED56, LED57, LED100, LED117, LED118, LED119, LED120, LED121, LED122, LED123, LED132, LED149, LED150, LED151, LED152, LED153, LED154, LED155: jaune; LED5MM
LED35, LED44, LED45, LED46, LED47, LED48, LED49, LED50, LED97, LED101, LED110, LED111, LED112, LED113, LED114, LED115, LED116, LED133, LED142, LED143, LED144, LED145, LED146, LED147, LED148: vert; LED5MM
LED36, LED58, LED59, LED60, LED61, LED62, LED63, LED64, LED98, LED102, LED124, LED125, LED126, LED127, LED128, LED129, LED130, LED134, LED156, LED157, LED158, LED159, LED160, LED161, LED162: bleu; LED5MM
LIPO: JST-12; GH-12-V
LIPO1: JST-04GH-V; GH-04-V
MOT_AR_D: 1X06
MOT_AR_G: 1X06
MOT_AV_D: 1X06
MOT_AV_G: 1X06
MOT_H: 1X06
MOT_V: 1X06
MULTI-BUTTON-1:C1, MULTI-BUTTON-2:C1: 1µF; C0805
MULTI-BUTTON-1:R1, MULTI-BUTTON-2:R1: 4k7; R0805
MULTI-BUTTON-1:R2, MULTI-BUTTON-2:R2: 2k2; R0805
MULTI-BUTTON-1:R3, MULTI-BUTTON-2:R3: 10k; R0805
MULTI-BUTTON-1:U1, MULTI-BUTTON-1:U2, MULTI-BUTTON-1:U3, MULTI-BUTTON-2:U1, MULTI-BUTTON-2:U2, MULTI-BUTTON-2:U3: PUSH-BUTTON
P1: RGEF800; 5MM
PHARES_ET_TOF_AV: JST-10; GH-10-V
Q1, Q2, Q3, Q4: BSS138; SOT23
R1, R45: 470; R0805
R2, R3, R6, R7, R8, R9, R35, R36, R37, R38: 10k; R0805
R4, R5, R10, R13, R14: 330; R0805
R11: 22k; R0805
R12: 6k8; R0805
R15, R17, R20, R22, R24, R26, R28, R30, R32, R34, R40, R42, R46, R47, R48, R49, R50, R51, R52, R53, R54, R55, R56, R57, R58, R63, R64, R65, R70, R71, R72, R73, R74, R75, R76, R77: 0; R0805
R16, R18, R19, R21, R23, R25, R27, R29, R31, R33, R39, R41, R59, R60, R61, R62, R66, R67, R68, R69, R78, R79, R80, R81: 270; R0805
R43: 220; R0805
R44, R82: 1k; R0805
RASPPBERRY_PI: 2X20/90
RPI: RPI-ZERO; RASPBERRYPI_BASTELSTUBE_V13_RASPI_BOARD_B+_FULL
S1: SWITCH_LPV-1
S2, S3: TL36PO; TL3XPO
T1, T2, T3, T4, T5, T6, T7, T8, T9, T10, T11, T12, T13, T14, T15, T16, T17, T18, T19, T20, T21, T22, T23, T24: SOT23-BEC
TOF_LP_D_AND_DISPLAY: JST-05; GH-05-V
TOF_LP_G: JST-05; GH-05-V
TOF_PINCE: JST-06; GH-06-V
U1: TEENSY_3.5_DIL+USB
U2: TEENSY_3.1-3.2_DIL; TEENSY_3.0-3.2&LC_DIL
U$1: TEENSY_3.1-3.2_DIL+4; TEENSY_3.0-3.2&LC_DIL+4
U$2, U$4: PUSH-BUTTON
U$3: WIZ820IO; WIZ820
USB_BACKUP_DEBUG: 1X03
XL320_D, XL320_G, XL320_G1, XL320_G2: DYNAMIXEL-1X03XL; DYNAMIXEL_XL_1X03

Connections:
3V3@1: R82.1, RPI.1
12V_AUX: C3.1, DC3.1, S1.3
+3V3: DC1.3, DELS_ET_TOF_AR.2, JUMPER.2, PHARES_ET_TOF_AV.2, Q1.1, Q2.1, R2.1, R5.1, R6.1, R8.1, R9.1, S3.3, U1.3.3V, U1.3.3V3, U2.3.3V, U$3.VIN1, U$3.VIN2
+3V3G: DC5.3, MULTI-BUTTON-1:R1.1, MULTI-BUTTON-2:R1.1, Q3.1, Q4.1, R35.1, R37.1, T11.C, T12.C, TOF_LP_D_AND_DISPLAY.2, TOF_LP_G.2, TOF_PINCE.2, U$1.3.3V
+3V3_LEDS: DC2.3, T1.C, T2.C, T3.C, T4.C, T5.C, T6.C, T7.C, T8.C, T9.C, T10.C
+5V: C11.1, ENCODEUR_DROIT.1, ENCODEUR_GAUCHE.1, H-BRIDGE_AR_D:C2.2, H-BRIDGE_AR_D:IC1.9, H-BRIDGE_AR_G:C2.2, H-BRIDGE_AR_G:IC1.9, H-BRIDGE_AV_D:C2.2, H-BRIDGE_AV_D:IC1.9, H-BRIDGE_AV_G:C2.2, H-BRIDGE_AV_G:IC1.9, IC3.2, MOT_AR_D.4, MOT_AR_G.4, MOT_AV_D.4, MOT_AV_G.4, R3.1, R7.1
+5VB: DC6.3, R44.1, RPI.2, RPI.4
+5VG: C16.1, H-BRIDGE1:C2.2, H-BRIDGE1:IC1.9, IC1.2, MOT_H.4, MOT_V.4, R36.1, R38.1
+5V_RPI: DC3.3, R1.2, RASPPBERRY_PI.2, RASPPBERRY_PI.4
+6V: C13.1, C17.1, DC-DC-6V.VOUT, F1.2, XL320_G1.VCC, XL320_G2.VCC
+6V5: C6.1, C7.1, DC4.3, XL320_D.VCC, XL320_G.VCC
+12V: ARRET_URGENCE.7, ARRET_URGENCE.8, ARRET_URGENCE.9, ARRET_URGENCE.10, ARRET_URGENCE.11, ARRET_URGENCE.12, AX12_D.DYN_VCC, AX12_G.DYN_VCC, C1.1, C2.1, C4.1, C5.1, C8.1, C9.1, DC1.1, DC2.1, DC4.1, GRUE.7, GRUE.8, GRUE.9, GRUE.10, H-BRIDGE_AR_D:C1.2, H-BRIDGE_AR_D:D2.C, H-BRIDGE_AR_D:D3.C, H-BRIDGE_AR_D:IC1.4, H-BRIDGE_AR_G:C1.2, H-BRIDGE_AR_G:D2.C, H-BRIDGE_AR_G:D3.C, H-BRIDGE_AR_G:IC1.4, H-BRIDGE_AV_D:C1.2, H-BRIDGE_AV_D:D2.C, H-BRIDGE_AV_D:D3.C, H-BRIDGE_AV_D:IC1.4, H-BRIDGE_AV_G:C1.2, H-BRIDGE_AV_G:D2.C, H-BRIDGE_AV_G:D3.C, H-BRIDGE_AV_G:IC1.4, IC3.3, R11.1
+12VB: C18.2, C19.2, DC6.1, DC7.1, S2.1
+12VG: AX12_G1.DYN_VCC, C12.1, C14.1, C15.1, DC5.1, DC-DC-6V.VIN, GRUE1.7, GRUE1.8, GRUE1.9, GRUE1.10, IC1.3
CHOOSE_COLOR: LED3.C, R4.2, S3.2, U1.A22
DEL_BLEU_1: LED134.A, LED156.A, LED157.A, LED158.A, LED159.A, LED160.A, LED161.A, LED162.A, T20.E
DEL_BLEU_1_PWM: R62.2, RPI.36
DEL_BLEU_2: LED36.A, LED58.A, LED59.A, LED60.A, LED61.A, LED62.A, LED63.A, LED64.A, T16.E
DEL_BLEU_2_PWM: R69.2, RPI.23
DEL_BLEU_3: LED102.A, LED124.A, LED125.A, LED126.A, LED127.A, LED128.A, LED129.A, LED130.A, T24.E
DEL_BLEU_3_PWM: R81.2, RPI.13
DEL_CLIGNOTANT_D: DELS_ET_TOF_AR.11, PHARES_ET_TOF_AV.9, R28.2
DEL_CLIGNOTANT_D_PWM: R27.1, U2.20/A6
DEL_CLIGNOTANT_G: DELS_ET_TOF_AR.12, PHARES_ET_TOF_AV.8, R26.2
DEL_CLIGNOTANT_G_PWM: R25.1, U2.10
DEL_FEUX_NUIT_AR: DELS_ET_TOF_AR.13, R30.2
DEL_FEUX_NUIT_AR_PWM: R29.1, U2.21/A7
DEL_FEUX_NUIT_AV: PHARES_ET_TOF_AV.10, R24.2
DEL_FEUX_NUIT_AV_PWM: R23.1, U2.9
DEL_FEUX_RECUL: DELS_ET_TOF_AR.15, R34.2
DEL_FEUX_RECUL_PWM: R33.1, U2.23/A9
DEL_FEUX_STOP: DELS_ET_TOF_AR.14, R32.2
DEL_FEUX_STOP_PWM: R31.1, U2.22/A8
DEL_GYRO_1: DEL_GYRO.2, R15.2
DEL_GYRO_1G: GYRO.1, R40.2
DEL_GYRO_1_PWM: R19.1, U2.6
DEL_GYRO_1_PWMG: R39.1, U$1.6
DEL_GYRO_2: DEL_GYRO.3, R17.2
DEL_GYRO_2G: GYRO.3, R42.2
DEL_GYRO_2_PWM: R16.1, U2.5
DEL_GYRO_2_PWMG: R41.1, U$1.20/A6
DEL_GYRO_3: DEL_GYRO.4, R20.2
DEL_GYRO_3_PWM: R18.1, U2.4
DEL_GYRO_4: DEL_GYRO.5, R22.2
DEL_GYRO_4_PWM: R21.1, U2.3
DEL_JAUNE_1: LED132.A, LED149.A, LED150.A, LED151.A, LED152.A, LED153.A, LED154.A, LED155.A, T19.E
DEL_JAUNE_1_PWM: R61.2, RPI.37
DEL_JAUNE_2: LED34.A, LED51.A, LED52.A, LED53.A, LED54.A, LED55.A, LED56.A, LED57.A, T15.E
DEL_JAUNE_2_PWM: R68.2, RPI.29
DEL_JAUNE_3: LED100.A, LED117.A, LED118.A, LED119.A, LED120.A, LED121.A, LED122.A, LED123.A, T23.E
DEL_JAUNE_3_PWM: R80.2, RPI.15
DEL_ORANGE_1: LED131.A, LED135.A, LED136.A, LED137.A, LED138.A, LED139.A, LED140.A, LED141.A, T17.E
DEL_ORANGE_1_PWM: R59.2, RPI.38
DEL_ORANGE_2: LED33.A, LED37.A, LED38.A, LED39.A, LED40.A, LED41.A, LED42.A, LED43.A, T13.E
DEL_ORANGE_2_PWM: R66.2, RPI.31
DEL_ORANGE_3: LED99.A, LED103.A, LED104.A, LED105.A, LED106.A, LED107.A, LED108.A, LED109.A, T21.E
DEL_ORANGE_3_PWM: R78.2, RPI.19
DEL_POWER: DC7.3, T13.C, T14.C, T15.C, T16.C, T17.C, T18.C, T19.C, T20.C, T21.C, T22.C, T23.C, T24.C
DEL_VERT_1: LED133.A, LED142.A, LED143.A, LED144.A, LED145.A, LED146.A, LED147.A, LED148.A, T18.E
DEL_VERT_1_PWM: R60.2, RPI.40
DEL_VERT_2: LED35.A, LED44.A, LED45.A, LED46.A, LED47.A, LED48.A, LED49.A, LED50.A, T14.E
DEL_VERT_2_PWM: R67.2, RPI.33
DEL_VERT_3: LED101.A, LED110.A, LED111.A, LED112.A, LED113.A, LED114.A, LED115.A, LED116.A, T22.E
DEL_VERT_3_PWM: R79.2, RPI.21
ENC_AR_D_A: MOT_AR_D.5, U1.30
ENC_AR_D_B: MOT_AR_D.6, U1.38/A19
ENC_AR_G_A: MOT_AR_G.5, U1.28
ENC_AR_G_B: MOT_AR_G.6, U1.29
ENC_AV_D_A: MOT_AV_D.5, U1.26
ENC_AV_D_B: MOT_AV_D.6, U1.27
ENC_AV_G_A: MOT_AV_G.5, U1.24
ENC_AV_G_B: MOT_AV_G.6, U1.25
ENC_D_A: ENCODEUR_DROIT.3, U1.18/A4
ENC_D_B: ENCODEUR_DROIT.4, U1.39/A20
ENC_G_A: ENCODEUR_GAUCHE.3, U1.16/A2
ENC_G_B: ENCODEUR_GAUCHE.4, U1.17/A3
ETH_MISO: U1.12, U$3.MISO
ETH_MOSI: U1.11, U$3.MOSI
ETH_RST: R8.2, U1.15/A1, U$3.RESET
ETH_SCLK: U1.13, U$3.SCLK
ETH_SS: U1.10, U$3.SS
GND: AX12_D.GND, AX12_G.GND, C1.2, C2.2, C3.2, C4.2, C5.2, C6.2, C7.2, C8.2, C9.2, C10.-, C11.2, DC1.2, DC2.2, DC3.2, DC4.2, DELS_ET_TOF_AR.1, DEL_GYRO.1, ENCODEUR_DROIT.2, ENCODEUR_GAUCHE.2, GRUE.3, GRUE.4, GRUE.5, GRUE.6, H-BRIDGE_AR_D:C1.1, H-BRIDGE_AR_D:C2.1, H-BRIDGE_AR_D:D1.A, H-BRIDGE_AR_D:D4.A, H-BRIDGE_AR_D:IC1.1, H-BRIDGE_AR_D:IC1.8, H-BRIDGE_AR_D:IC1.15, H-BRIDGE_AR_D:R1.2, H-BRIDGE_AR_D:R2.2, H-BRIDGE_AR_D:R3.2, H-BRIDGE_AR_G:C1.1, H-BRIDGE_AR_G:C2.1, H-BRIDGE_AR_G:D1.A, H-BRIDGE_AR_G:D4.A, H-BRIDGE_AR_G:IC1.1, H-BRIDGE_AR_G:IC1.8, H-BRIDGE_AR_G:IC1.15, H-BRIDGE_AR_G:R1.2, H-BRIDGE_AR_G:R2.2, H-BRIDGE_AR_G:R3.2, H-BRIDGE_AV_D:C1.1, H-BRIDGE_AV_D:C2.1, H-BRIDGE_AV_D:D1.A, H-BRIDGE_AV_D:D4.A, H-BRIDGE_AV_D:IC1.1, H-BRIDGE_AV_D:IC1.8, H-BRIDGE_AV_D:IC1.15, H-BRIDGE_AV_D:R1.2, H-BRIDGE_AV_D:R2.2, H-BRIDGE_AV_D:R3.2, H-BRIDGE_AV_G:C1.1, H-BRIDGE_AV_G:C2.1, H-BRIDGE_AV_G:D1.A, H-BRIDGE_AV_G:D4.A, H-BRIDGE_AV_G:IC1.1, H-BRIDGE_AV_G:IC1.8, H-BRIDGE_AV_G:IC1.15, H-BRIDGE_AV_G:R1.2, H-BRIDGE_AV_G:R2.2, H-BRIDGE_AV_G:R3.2, IC3.1, JUMPER.1, LED1.C, LED2.C, LED4.C, LED5.C, LED6.C, LIPO.1, LIPO.2, LIPO.3, LIPO.4, LIPO.5, LIPO.6, MOT_AR_D.3, MOT_AR_G.3, MOT_AV_D.3, MOT_AV_G.3, PHARES_ET_TOF_AV.1, R12.2, RASPPBERRY_PI.6, RASPPBERRY_PI.9, RASPPBERRY_PI.14, RASPPBERRY_PI.20, RASPPBERRY_PI.25, RASPPBERRY_PI.30, RASPPBERRY_PI.34, RASPPBERRY_PI.39, S1.B, S1.B1, S3.1, U1.AGND, U1.GND, U1.GND1, U2.AGND, U2.GND, U$2.1, U$2.2, U$3.GND1, U$3.GND2, U$3.GND3, U$3.PWDN, USB_BACKUP_DEBUG.1, XL320_D.GND, XL320_G.GND
GNDB: C18.1, C19.1, C20.1, DC6.2, DC7.2, DEBUG_UART.1, LED97.K, LED98.K, LIPO1.1, LIPO1.2, R46.2, R47.2, R48.2, R49.2, R50.2, R51.2, R52.2, R53.2, R54.2, R55.2, R56.2, R57.2, R58.2, R63.2, R64.2, R65.2, R70.2, R71.2, R72.2, R73.2, R74.2, R75.2, R76.2, R77.2, RPI.6, RPI.9, RPI.14, RPI.20, RPI.25, RPI.30, RPI.34, RPI.39, U$4.3, U$4.4
GNDG: AX12_G1.GND, C12.2, C13.2, C14.2, C15.2, C16.2, C17.2, DC5.2, DC-DC-6V.GND, GRUE1.3, GRUE1.4, GRUE1.5, GRUE1.6, GYRO.2, GYRO.4, H-BRIDGE1:C1.1, H-BRIDGE1:C2.1, H-BRIDGE1:D1.A, H-BRIDGE1:D4.A, H-BRIDGE1:D5.A, H-BRIDGE1:D8.A, H-BRIDGE1:IC1.1, H-BRIDGE1:IC1.8, H-BRIDGE1:IC1.15, H-BRIDGE1:R1.2, H-BRIDGE1:R2.2, H-BRIDGE1:R3.2, H-BRIDGE1:R4.2, H-BRIDGE1:R5.2, H-BRIDGE1:R6.2, IC1.1, MOT_H.3, MOT_V.3, MULTI-BUTTON-1:C1.1, MULTI-BUTTON-1:R2.2, MULTI-BUTTON-1:R3.2, MULTI-BUTTON-1:U3.3, MULTI-BUTTON-1:U3.4, MULTI-BUTTON-2:C1.1, MULTI-BUTTON-2:R2.2, MULTI-BUTTON-2:R3.2, MULTI-BUTTON-2:U3.3, MULTI-BUTTON-2:U3.4, R43.1, TOF_LP_D_AND_DISPLAY.1, TOF_LP_G.1, TOF_PINCE.1, U$1.AGND, U$1.GND, XL320_G1.GND, XL320_G2.GND
GRUE_SERIAL_MISO: GRUE.2, U1.0
GRUE_SERIAL_MISOG: GRUE1.2, U$1.1
GRUE_SERIAL_MOSI: GRUE.1, U1.1
GRUE_SERIAL_MOSIG: GRUE1.1, U$1.0
JUMPER: JUMPER.3, U1.19/A5
MOT_AR_D_EN: H-BRIDGE_AR_D:IC1.6, H-BRIDGE_AR_D:IC1.11, H-BRIDGE_AR_D:R1.1, U1.35/A16
MOT_AR_D_IN1: H-BRIDGE_AR_D:IC1.5, H-BRIDGE_AR_D:IC1.12, H-BRIDGE_AR_D:R2.1, U1.36/A17
MOT_AR_D_IN2: H-BRIDGE_AR_D:IC1.7, H-BRIDGE_AR_D:IC1.10, H-BRIDGE_AR_D:R3.1, U1.37/A18
MOT_AR_D_OUT+: H-BRIDGE_AR_D:D1.C, H-BRIDGE_AR_D:D2.A, H-BRIDGE_AR_D:IC1.2, H-BRIDGE_AR_D:IC1.14, MOT_AR_D.1
MOT_AR_D_OUT-: H-BRIDGE_AR_D:D3.A, H-BRIDGE_AR_D:D4.C, H-BRIDGE_AR_D:IC1.3, H-BRIDGE_AR_D:IC1.13, MOT_AR_D.2
MOT_AR_G_EN: H-BRIDGE_AR_G:IC1.6, H-BRIDGE_AR_G:IC1.11, H-BRIDGE_AR_G:R1.1, U1.21/A7
MOT_AR_G_IN1: H-BRIDGE_AR_G:IC1.5, H-BRIDGE_AR_G:IC1.12, H-BRIDGE_AR_G:R2.1, U1.22/A8
MOT_AR_G_IN2: H-BRIDGE_AR_G:IC1.7, H-BRIDGE_AR_G:IC1.10, H-BRIDGE_AR_G:R3.1, U1.23/A9
MOT_AR_G_OUT+: H-BRIDGE_AR_G:D1.C, H-BRIDGE_AR_G:D2.A, H-BRIDGE_AR_G:IC1.2, H-BRIDGE_AR_G:IC1.14, MOT_AR_G.1
MOT_AR_G_OUT-: H-BRIDGE_AR_G:D3.A, H-BRIDGE_AR_G:D4.C, H-BRIDGE_AR_G:IC1.3, H-BRIDGE_AR_G:IC1.13, MOT_AR_G.2
MOT_AV_D_EN: H-BRIDGE_AV_D:IC1.6, H-BRIDGE_AV_D:IC1.11, H-BRIDGE_AV_D:R1.1, U1.5
MOT_AV_D_IN1: H-BRIDGE_AV_D:IC1.5, H-BRIDGE_AV_D:IC1.12, H-BRIDGE_AV_D:R2.1, U1.6
MOT_AV_D_IN2: H-BRIDGE_AV_D:IC1.7, H-BRIDGE_AV_D:IC1.10, H-BRIDGE_AV_D:R3.1, U1.9
MOT_AV_D_OUT+: H-BRIDGE_AV_D:D1.C, H-BRIDGE_AV_D:D2.A, H-BRIDGE_AV_D:IC1.2, H-BRIDGE_AV_D:IC1.14, MOT_AV_D.1
MOT_AV_D_OUT-: H-BRIDGE_AV_D:D3.A, H-BRIDGE_AV_D:D4.C, H-BRIDGE_AV_D:IC1.3, H-BRIDGE_AV_D:IC1.13, MOT_AV_D.2
MOT_AV_G_EN: H-BRIDGE_AV_G:IC1.6, H-BRIDGE_AV_G:IC1.11, H-BRIDGE_AV_G:R1.1, U1.2
MOT_AV_G_IN1: H-BRIDGE_AV_G:IC1.5, H-BRIDGE_AV_G:IC1.12, H-BRIDGE_AV_G:R2.1, U1.3
MOT_AV_G_IN2: H-BRIDGE_AV_G:IC1.7, H-BRIDGE_AV_G:IC1.10, H-BRIDGE_AV_G:R3.1, U1.4
MOT_AV_G_OUT+: H-BRIDGE_AV_G:D1.C, H-BRIDGE_AV_G:D2.A, H-BRIDGE_AV_G:IC1.2, H-BRIDGE_AV_G:IC1.14, MOT_AV_G.1
MOT_AV_G_OUT-: H-BRIDGE_AV_G:D3.A, H-BRIDGE_AV_G:D4.C, H-BRIDGE_AV_G:IC1.3, H-BRIDGE_AV_G:IC1.13, MOT_AV_G.2
MOT_H_EN: H-BRIDGE1:IC1.6, H-BRIDGE1:R1.1, U$1.3
MOT_H_ENC_A: MOT_H.5, U$1.11
MOT_H_ENC_B: MOT_H.6, U$1.12
MOT_H_IN1: H-BRIDGE1:IC1.5, H-BRIDGE1:R3.1, U$1.4
MOT_H_IN2: H-BRIDGE1:IC1.7, H-BRIDGE1:R4.1, U$1.5
MOT_H_OUT+: H-BRIDGE1:D1.C, H-BRIDGE1:D2.A, H-BRIDGE1:IC1.2, MOT_H.1
MOT_H_OUT-: H-BRIDGE1:D3.A, H-BRIDGE1:D4.C, H-BRIDGE1:IC1.3, MOT_H.2
MOT_V_EN: H-BRIDGE1:IC1.11, H-BRIDGE1:R2.1, U$1.21/A7
MOT_V_ENC_A: MOT_V.5, U$1.15/A1
MOT_V_ENC_B: MOT_V.6, U$1.16/A2
MOT_V_IN1: H-BRIDGE1:IC1.10, H-BRIDGE1:R5.1, U$1.22/A8
MOT_V_IN2: H-BRIDGE1:IC1.12, H-BRIDGE1:R6.1, U$1.23/A9
MOT_V_OUT+: H-BRIDGE1:D5.C, H-BRIDGE1:D6.A, H-BRIDGE1:IC1.13, MOT_V.1
MOT_V_OUT-: H-BRIDGE1:D7.A, H-BRIDGE1:D8.C, H-BRIDGE1:IC1.14, MOT_V.2
MULTI-BUTTON-1:N$3: MULTI-BUTTON-1:R2.1, MULTI-BUTTON-1:U2.3, MULTI-BUTTON-1:U2.4
MULTI-BUTTON-1:N$4: MULTI-BUTTON-1:R3.1, MULTI-BUTTON-1:U1.3, MULTI-BUTTON-1:U1.4
MULTI-BUTTON-2:N$3: MULTI-BUTTON-2:R2.1, MULTI-BUTTON-2:U2.3, MULTI-BUTTON-2:U2.4
MULTI-BUTTON-2:N$4: MULTI-BUTTON-2:R3.1, MULTI-BUTTON-2:U1.3, MULTI-BUTTON-2:U1.4
unnamed: LED1.A, R1.1
unnamed: R9.2, RASPPBERRY_PI.29, U$2.3, U$2.4
unnamed: ARRET_URGENCE.1, ARRET_URGENCE.2, ARRET_URGENCE.3, ARRET_URGENCE.4, ARRET_URGENCE.5, ARRET_URGENCE.6, C10.+, D1.-, S1.2
unnamed: D1.+1, D1.+2, P1.P$1
unnamed: R10.1, RASPPBERRY_PI.31
unnamed: U1.33/A14, U2.0
unnamed: LED2.A, R4.1
unnamed: LED3.A, R5.2
unnamed: LIPO.7, LIPO.8, LIPO.9, LIPO.10, LIPO.11, LIPO.12, P1.P$2
unnamed: U1.34/A15, U2.1
unnamed: LED4.A, R10.2
unnamed: R11.2, R12.1, U1.A21
unnamed: LED6.A, R14.1
unnamed: LED5.A, R13.1
unnamed: R13.2, U1.14/A0
unnamed: R14.2, U1.20/A6
unnamed: R15.1, T3.E
unnamed: R19.2, T3.B
unnamed: R40.1, T11.E
unnamed: R39.2, T11.B
unnamed: R17.1, T1.E
unnamed: R16.2, T1.B
unnamed: R42.1, T12.E
unnamed: R41.2, T12.B
unnamed: R20.1, T2.E
unnamed: R18.2, T2.B
unnamed: DC-DC-6V.TRIM+, R43.2
unnamed: MULTI-BUTTON-1:C1.2, MULTI-BUTTON-1:R1.2, MULTI-BUTTON-1:U1.1, MULTI-BUTTON-1:U1.2, MULTI-BUTTON-1:U2.1, MULTI-BUTTON-1:U2.2, MULTI-BUTTON-1:U3.1, MULTI-BUTTON-1:U3.2, U$1.A10
unnamed: R22.1, T4.E
unnamed: R21.2, T4.B
unnamed: MULTI-BUTTON-2:C1.2, MULTI-BUTTON-2:R1.2, MULTI-BUTTON-2:U1.1, MULTI-BUTTON-2:U1.2, MULTI-BUTTON-2:U2.1, MULTI-BUTTON-2:U2.2, MULTI-BUTTON-2:U3.1, MULTI-BUTTON-2:U3.2, U$1.A11
unnamed: F1.1, H-BRIDGE1:C1.2, H-BRIDGE1:D2.C, H-BRIDGE1:D3.C, H-BRIDGE1:D6.C, H-BRIDGE1:D7.C, H-BRIDGE1:IC1.4
unnamed: R24.1, T5.E
unnamed: R23.2, T5.B
unnamed: F2.1, LIPO1.3, LIPO1.4
unnamed: D2.A, F2.2
unnamed: R26.1, T6.E
unnamed: R25.2, T6.B
unnamed: D2.C, S2.2
unnamed: LED97.A, R44.2
unnamed: R28.1, T7.E
unnamed: R27.2, T7.B
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

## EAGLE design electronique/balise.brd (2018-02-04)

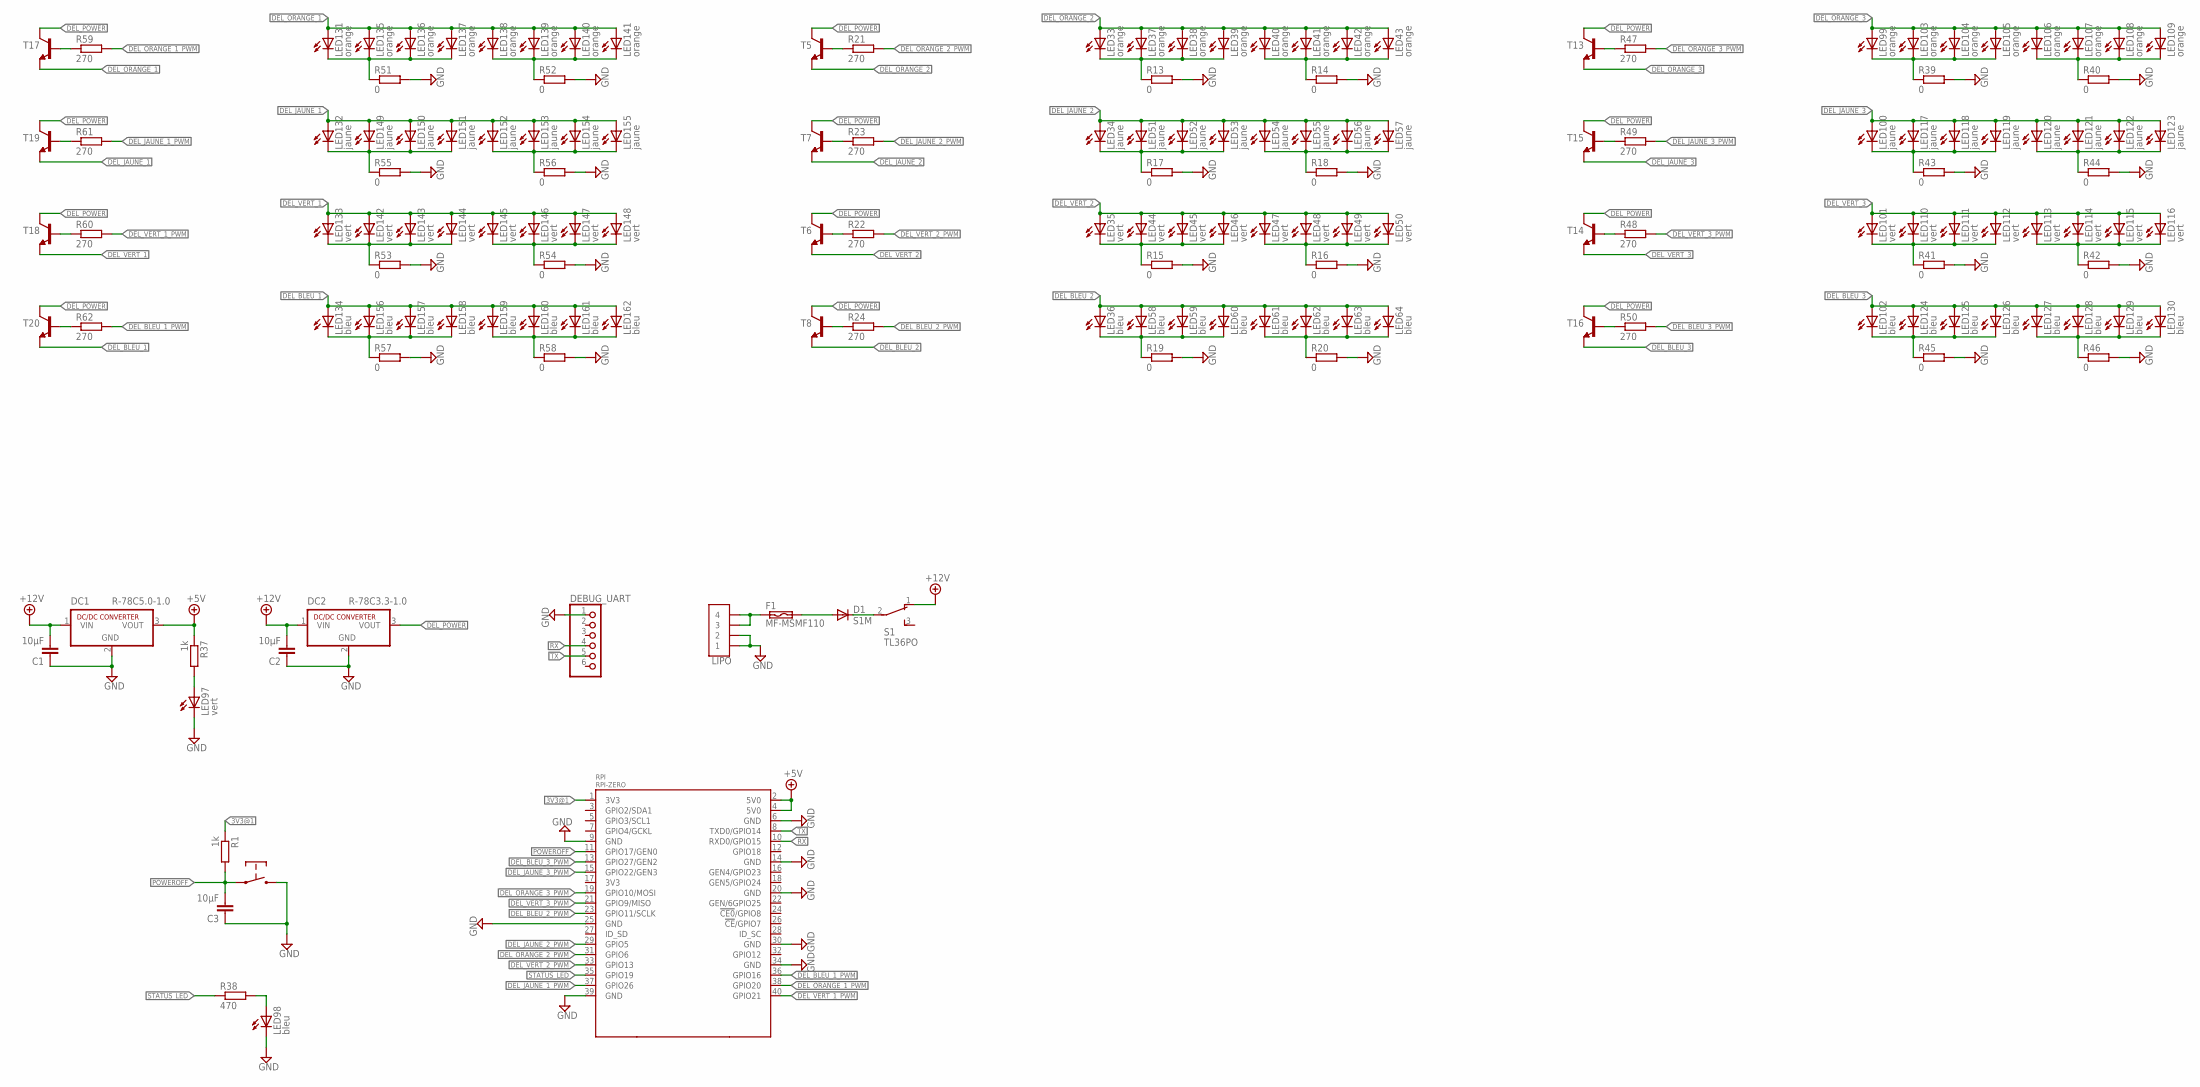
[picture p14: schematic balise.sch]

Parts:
C1, C2, C3: 10µF; C0805
D1: S1M; SMA
DC1: R-78C5.0-1.0; SIP3
DC2: R-78C3.3-1.0; SIP3
DEBUG_UART: PINHD-1X6; 1X06
F1: MF-MSMF110
LED33, LED37, LED38, LED39, LED40, LED41, LED42, LED43, LED99, LED103, LED104, LED105, LED106, LED107, LED108, LED109, LED131, LED135, LED136, LED137, LED138, LED139, LED140, LED141: orange; LED5MM
LED34, LED51, LED52, LED53, LED54, LED55, LED56, LED57, LED100, LED117, LED118, LED119, LED120, LED121, LED122, LED123, LED132, LED149, LED150, LED151, LED152, LED153, LED154, LED155: jaune; LED5MM
LED35, LED44, LED45, LED46, LED47, LED48, LED49, LED50, LED97, LED101, LED110, LED111, LED112, LED113, LED114, LED115, LED116, LED133, LED142, LED143, LED144, LED145, LED146, LED147, LED148: vert; LED5MM
LED36, LED58, LED59, LED60, LED61, LED62, LED63, LED64, LED98, LED102, LED124, LED125, LED126, LED127, LED128, LED129, LED130, LED134, LED156, LED157, LED158, LED159, LED160, LED161, LED162: bleu; LED5MM
LIPO: JST-04GH-V; GH-04-V
R1, R37: 1k; R0805
R13, R14, R15, R16, R17, R18, R19, R20, R39, R40, R41, R42, R43, R44, R45, R46, R51, R52, R53, R54, R55, R56, R57, R58: 0; R0805
R21, R22, R23, R24, R47, R48, R49, R50, R59, R60, R61, R62: 270; R0805
R38: 470; R0805
RPI: RPI-ZERO; RASPBERRYPI_BASTELSTUBE_V13_RASPI_BOARD_B+_FULL
S1: TL36PO; TL3XPO
T5, T6, T7, T8, T13, T14, T15, T16, T17, T18, T19, T20: BC817-16-NPN-SOT23-BEC; SOT23-BEC
U$1: PUSH-BUTTON

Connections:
3V3@1: R1.1, RPI.1 (3V3)
+5V: DC1.3 (VOUT), R37.1, RPI.2 (5V0), RPI.4 (5V0)
+12V: C1.2, C2.2, DC1.1 (VIN), DC2.1 (VIN), S1.1 (O)
DEL_BLEU_1: LED134.A, LED156.A, LED157.A, LED158.A, LED159.A, LED160.A, LED161.A, LED162.A, T20.E
DEL_BLEU_1_PWM: R62.2, RPI.36 (GPIO16)
DEL_BLEU_2: LED36.A, LED58.A, LED59.A, LED60.A, LED61.A, LED62.A, LED63.A, LED64.A, T8.E
DEL_BLEU_2_PWM: R24.2, RPI.23 (GPIO11/SCLK)
DEL_BLEU_3: LED102.A, LED124.A, LED125.A, LED126.A, LED127.A, LED128.A, LED129.A, LED130.A, T16.E
DEL_BLEU_3_PWM: R50.2, RPI.13 (GPIO27/GEN2)
DEL_JAUNE_1: LED132.A, LED149.A, LED150.A, LED151.A, LED152.A, LED153.A, LED154.A, LED155.A, T19.E
DEL_JAUNE_1_PWM: R61.2, RPI.37 (GPIO26)
DEL_JAUNE_2: LED34.A, LED51.A, LED52.A, LED53.A, LED54.A, LED55.A, LED56.A, LED57.A, T7.E
DEL_JAUNE_2_PWM: R23.2, RPI.29 (GPIO5)
DEL_JAUNE_3: LED100.A, LED117.A, LED118.A, LED119.A, LED120.A, LED121.A, LED122.A, LED123.A, T15.E
DEL_JAUNE_3_PWM: R49.2, RPI.15 (GPIO22/GEN3)
DEL_ORANGE_1: LED131.A, LED135.A, LED136.A, LED137.A, LED138.A, LED139.A, LED140.A, LED141.A, T17.E
DEL_ORANGE_1_PWM: R59.2, RPI.38 (GPIO20)
DEL_ORANGE_2: LED33.A, LED37.A, LED38.A, LED39.A, LED40.A, LED41.A, LED42.A, LED43.A, T5.E
DEL_ORANGE_2_PWM: R21.2, RPI.31 (GPIO6)
DEL_ORANGE_3: LED99.A, LED103.A, LED104.A, LED105.A, LED106.A, LED107.A, LED108.A, LED109.A, T13.E
DEL_ORANGE_3_PWM: R47.2, RPI.19 (GPIO10/MOSI)
DEL_POWER: DC2.3 (VOUT), T5.C, T6.C, T7.C, T8.C, T13.C, T14.C, T15.C, T16.C, T17.C, T18.C, T19.C, T20.C
DEL_VERT_1: LED133.A, LED142.A, LED143.A, LED144.A, LED145.A, LED146.A, LED147.A, LED148.A, T18.E
DEL_VERT_1_PWM: R60.2, RPI.40 (GPIO21)
DEL_VERT_2: LED35.A, LED44.A, LED45.A, LED46.A, LED47.A, LED48.A, LED49.A, LED50.A, T6.E
DEL_VERT_2_PWM: R22.2, RPI.33 (GPIO13)
DEL_VERT_3: LED101.A, LED110.A, LED111.A, LED112.A, LED113.A, LED114.A, LED115.A, LED116.A, T14.E
DEL_VERT_3_PWM: R48.2, RPI.21 (GPIO9/MISO)
GND: C1.1, C2.1, C3.1, DC1.2 (GND), DC2.2 (GND), DEBUG_UART.1, LED97.K (C), LED98.K (C), LIPO.1, LIPO.2, R13.2, R14.2, R15.2, R16.2, R17.2, R18.2, R19.2, R20.2, R39.2, R40.2, R41.2, R42.2, R43.2, R44.2, R45.2, R46.2, R51.2, R52.2, R53.2, R54.2, R55.2, R56.2, R57.2, R58.2, RPI.6 (GND), RPI.9 (GND), RPI.14 (GND), RPI.20 (GND), RPI.25 (GND), RPI.30 (GND), RPI.34 (GND), RPI.39 (GND), U$1.3, U$1.4
unnamed: F1.1, LIPO.3, LIPO.4
unnamed: D1.A, F1.2
unnamed: D1.C, S1.2
unnamed: LED33.K (C), LED37.K (C), LED38.K (C), LED39.K (C), R13.1
unnamed: LED40.K (C), LED41.K (C), LED42.K (C), LED43.K (C), R14.1
unnamed: LED35.K (C), LED44.K (C), LED45.K (C), LED46.K (C), R15.1
unnamed: LED47.K (C), LED48.K (C), LED49.K (C), LED50.K (C), R16.1
unnamed: LED34.K (C), LED51.K (C), LED52.K (C), LED53.K (C), R17.1
unnamed: LED54.K (C), LED55.K (C), LED56.K (C), LED57.K (C), R18.1
unnamed: LED36.K (C), LED58.K (C), LED59.K (C), LED60.K (C), R19.1
unnamed: LED61.K (C), LED62.K (C), LED63.K (C), LED64.K (C), R20.1
unnamed: R21.1, T5.B
unnamed: R22.1, T6.B
unnamed: R23.1, T7.B
unnamed: R24.1, T8.B
unnamed: LED97.A, R37.2
unnamed: LED98.A, R38.2
unnamed: LED99.K (C), LED103.K (C), LED104.K (C), LED105.K (C), R39.1
unnamed: LED106.K (C), LED107.K (C), LED108.K (C), LED109.K (C), R40.1
unnamed: LED101.K (C), LED110.K (C), LED111.K (C), LED112.K (C), R41.1
unnamed: LED113.K (C), LED114.K (C), LED115.K (C), LED116.K (C), R42.1
unnamed: LED100.K (C), LED117.K (C), LED118.K (C), LED119.K (C), R43.1
unnamed: LED120.K (C), LED121.K (C), LED122.K (C), LED123.K (C), R44.1
unnamed: LED102.K (C), LED124.K (C), LED125.K (C), LED126.K (C), R45.1
unnamed: LED127.K (C), LED128.K (C), LED129.K (C), LED130.K (C), R46.1
unnamed: R47.1, T13.B
unnamed: R48.1, T14.B
unnamed: R49.1, T15.B
unnamed: R50.1, T16.B
unnamed: LED131.K (C), LED135.K (C), LED136.K (C), LED137.K (C), R51.1
unnamed: LED138.K (C), LED139.K (C), LED140.K (C), LED141.K (C), R52.1
unnamed: LED133.K (C), LED142.K (C), LED143.K (C), LED144.K (C), R53.1
unnamed: LED145.K (C), LED146.K (C), LED147.K (C), LED148.K (C), R54.1
unnamed: LED132.K (C), LED149.K (C), LED150.K (C), LED151.K (C), R55.1
unnamed: LED152.K (C), LED153.K (C), LED154.K (C), LED155.K (C), R56.1
unnamed: LED134.K (C), LED156.K (C), LED157.K (C), LED158.K (C), R57.1
unnamed: LED159.K (C), LED160.K (C), LED161.K (C), LED162.K (C), R58.1
unnamed: R59.1, T17.B
unnamed: R60.1, T18.B
unnamed: R61.1, T19.B
unnamed: R62.1, T20.B
POWEROFF: C3.2, R1.2, RPI.11 (GPIO17/GEN0), U$1.1, U$1.2
RX: DEBUG_UART.4, RPI.10 (RXD0/GPIO15)
STATUS_LED: R38.1, RPI.35 (GPIO19)
TX: DEBUG_UART.5, RPI.8 (TXD0/GPIO14)

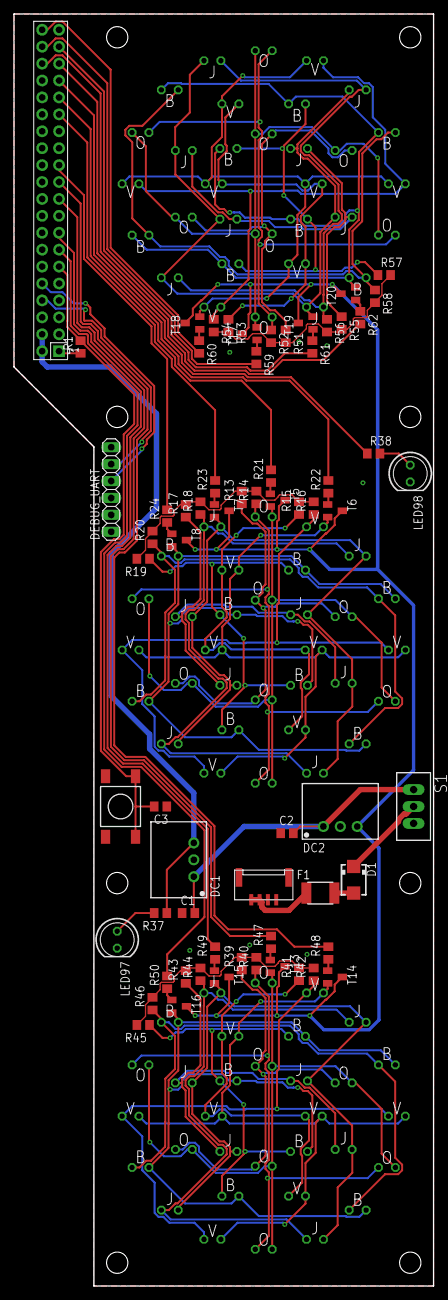
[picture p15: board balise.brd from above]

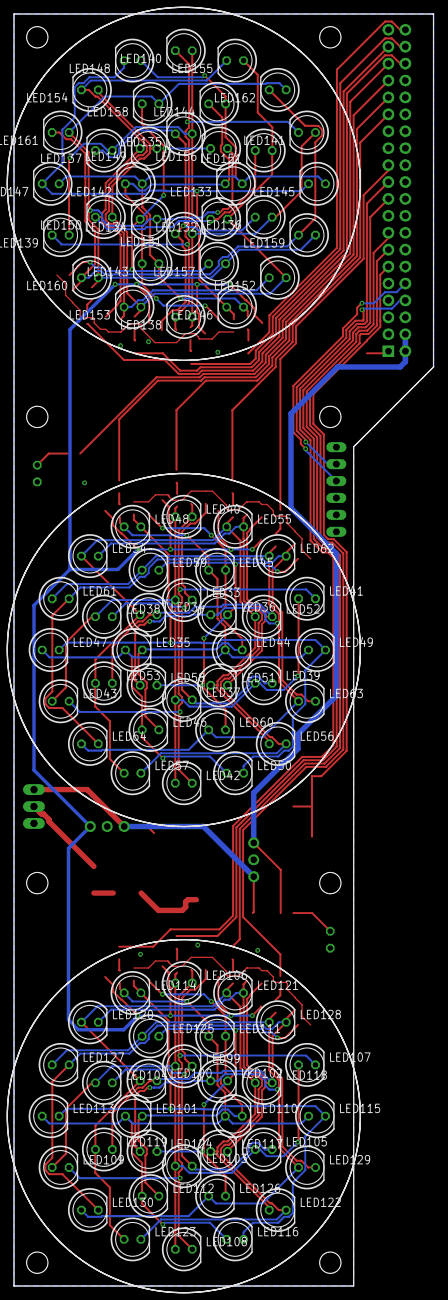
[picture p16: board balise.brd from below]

Board: 2 copper layers, 63.0 x 191.0 mm, 161 parts (96 on the bottom side), 74 nets.

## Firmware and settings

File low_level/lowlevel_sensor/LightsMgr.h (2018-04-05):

#ifndef _LIGHTS_MGR_h
#define _LIGHTS_MGR_h

#if defined(ARDUINO) && ARDUINO >= 100
	#include "Arduino.h"
#else
	#include "WProgram.h"
#endif

#include "config.h"

#define DEFAULT_BLINK_DURATION  500 // ms
#define ALARM_BLINK_DURATION    100 // ms
#define DEFAULT_TOGGLE_DELAY    50 // ms


typedef uint8_t LightningMode;
enum LightId
{
    ALL_OFF             = 0,
    TURN_LEFT           = 1,
    TURN_RIGHT          = 2,
    FLASHING            = 4,
    STOP_LIGHT          = 8,
    REVERSE_LIGHT       = 16,
    NIGHT_LIGHT_LOW     = 32,
    NIGHT_LIGHT_HIGH    = 64,
    ALARM_LIGHT         = 128
};


class Led
{
public:
    Led(uint8_t aPin, float aToggleDelay = DEFAULT_TOGGLE_DELAY)
    {
        pin = aPin;
        aimState = false;
        power = 255;
        currentPWM = 0;
        toggleDelay = aToggleDelay;
        lastUpdateTime = 0;
        blinkOnDuration = 0;
        blinkOffDuration = 0;
        lastBlinkTime = 0;
        pinMode(pin, OUTPUT);
        analogWrite(pin, 0);
    }

    void turnOn(uint8_t aPower = 255)
    {
        aimState = true;
        power = aPower;
        blinkOnDuration = 0;
        blinkOffDuration = 0;
    }

    void forceOn(uint8_t aPower = 255)
    {
        turnOn(aPower);
        currentPWM = (int32_t)aPower;
        analogWrite(pin, (uint8_t)currentPWM);
    }

    void turnOff()
    {
        aimState = false;
        blinkOnDuration = 0;
        blinkOffDuration = 0;
    }

    void forceOff()
    {
        turnOff();
        currentPWM = 0;
        analogWrite(pin, 0);
    }

    void blink(uint32_t onDuration, uint32_t offDuration)
    {
        if (blinkOnDuration == 0 || blinkOffDuration == 0)
        {
            lastBlinkTime = millis();
        }
        blinkOnDuration = onDuration;
        blinkOffDuration = offDuration;
    }

    void update()
    {
        uint32_t now = millis();

        if (blinkOnDuration > 0 && blinkOffDuration > 0)
        {
            if (aimState && now - lastBlinkTime > blinkOnDuration)
            {
                aimState = false;
                lastBlinkTime += blinkOnDuration;
            }
            else if (!aimState && now - lastBlinkTime > blinkOffDuration)
            {
                aimState = true;
                lastBlinkTime += blinkOffDuration;
            }
        }

        float increment = (float)power * (float)(now - lastUpdateTime) / toggleDelay;
        lastUpdateTime = now;
        if (aimState)
        {
            currentPWM += (int32_t)increment;
        }
        else
        {
            currentPWM -= (int32_t)increment;
        }
        currentPWM = constrain(currentPWM, 0, (int32_t)power);
        analogWrite(pin, (uint8_t)currentPWM);
    }

private:
    uint8_t pin;
    bool aimState;
    uint8_t power;
    int32_t currentPWM;
    float toggleDelay;
    uint32_t lastUpdateTime;
    uint32_t blinkOnDuration;  // ms
    uint32_t blinkOffDuration; // ms
    uint32_t lastBlinkTime;
};


class FlashingLight
{
public:
    FlashingLight(uint8_t pin1, uint8_t pin2, uint8_t pin3, uint8_t pin4):
        led1(pin1, 150),
        led2(pin2, 150),
        led3(pin3, 150),
        led4(pin4, 150),
        delayToPropagate(150),
        blinkOn(150),
        blinkOff(350)
    {
        lastStartTime = 0;
        phase = 0;
    }

    void turnOn()
    {
        phase = 1;
        led1.blink(blinkOn, blinkOff);
        lastStartTime = millis();
    }

    void turnOff()
    {
        phase = 0;
        led1.turnOff();
        led2.turnOff();
        led3.turnOff();
        led4.turnOff();
    }

    void update()
    {
        uint32_t now = millis();
        if (now - lastStartTime > delayToPropagate)
        {
            if (phase == 1)
            {
                led2.blink(blinkOn, blinkOff);
                phase = 2;
            }
            else if (phase == 2)
            {
                led3.blink(blinkOn, blinkOff);
                phase = 3;
            }
            else if (phase == 3)
            {
                led4.blink(blinkOn, blinkOff);
                phase = 4;
            }
            lastStartTime = now;
        }
        led1.update();
        led2.update();
        led3.update();
        led4.update();
    }

private:
    Led led1;
    Led led2;
    Led led3;
    Led led4;
    const uint32_t delayToPropagate;  // ms
    uint32_t lastStartTime;     // ms
    uint8_t phase;
    const uint32_t blinkOn;     // ms
    const uint32_t blinkOff;    // ms
};


class LightsMgr
{
public:
    LightsMgr() :
        ledTurnLeft(PIN_DEL_CLIGNO_G),
        ledTurnRight(PIN_DEL_CLIGNO_D),
        flashingLight(PIN_DEL_GYRO_1, PIN_DEL_GYRO_2, PIN_DEL_GYRO_3, PIN_DEL_GYRO_4),
        ledStop(PIN_DEL_STOP),
        ledReverse(PIN_DEL_RECUL),
        ledNightFront(PIN_DEL_NUIT_AV),
        ledNightBack(PIN_DEL_NUIT_AR)
    {
        analogWriteResolution(8);
    }

    void setLightningMode(LightningMode mode)
    {
        if (mode & ALARM_LIGHT)
        {
            ledTurnLeft.blink(ALARM_BLINK_DURATION, ALARM_BLINK_DURATION);
            ledTurnRight.blink(ALARM_BLINK_DURATION, ALARM_BLINK_DURATION);
        }
        else
        {
            if (mode & TURN_LEFT)
            {
                ledTurnLeft.blink(DEFAULT_BLINK_DURATION, DEFAULT_BLINK_DURATION);
            }
            else
            {
                ledTurnLeft.turnOff();
            }
            if (mode & TURN_RIGHT)
            {
                ledTurnRight.blink(DEFAULT_BLINK_DURATION, DEFAULT_BLINK_DURATION);
            }
            else
            {
                ledTurnRight.turnOff();
            }
        }
        if (mode & REVERSE_LIGHT)
        {
            ledReverse.turnOn();
        }
        else
        {
            ledReverse.turnOff();
        }
        if (mode & NIGHT_LIGHT_HIGH)
        {
            ledNightFront.turnOn();
            ledNightBack.turnOn(64);
        }
        else if (mode & NIGHT_LIGHT_LOW)
        {
            ledNightFront.turnOn(32);
            ledNightBack.turnOn(64);
        }
        else
        {
            ledNightFront.turnOff();
            ledNightBack.turnOff();
        }
        if (mode & STOP_LIGHT)
        {
            ledStop.turnOn();
            ledNightBack.turnOn();
        }
        else
        {
            ledStop.turnOff();
        }
        if (mode & FLASHING)
        {
            flashingLight.turnOn();
        }
        else
        {
            flashingLight.turnOff();
        }
    }

    void update()
    {
        ledTurnLeft.update();
        ledTurnRight.update();
        flashingLight.update();
        ledStop.update();
        ledReverse.update();
        ledNightFront.update();
        ledNightBack.update();
    }

    void infoSignalOn()
    {
        ledTurnLeft.forceOn();
        ledTurnRight.forceOn();
    }

    void infoSignalOff()
    {
        ledTurnLeft.forceOff();
        ledTurnRight.forceOff();
    }

private:
    Led ledTurnLeft;
    Led ledTurnRight;
    FlashingLight flashingLight;
    Led ledStop;
    Led ledReverse;
    Led ledNightFront;
    Led ledNightBack;
};


#endif

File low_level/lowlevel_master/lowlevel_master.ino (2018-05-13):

/*
 Name:		lowlevel_master.ino
 Created:	04/03/2018 20:10:42
 Author:	Sylvain Gaultier
*/

#include "Config/pin_mapping.h"
#include "CommunicationServer/OrderMgr.h"
#include "Locomotion/MotionControlSystem.h"
#include "Locomotion/ContextualLightning.h"
#include "SlaveCommunication/SlaveSensorLed.h"
#include "SlaveCommunication/SlaveActuator.h"
#include "CommunicationServer/Serializer.h"

#define ODOMETRY_REPORT_PERIOD  20  // ms


void setup()
{
    pinMode(PIN_DEL_STATUS_1, OUTPUT);
    pinMode(PIN_DEL_STATUS_2, OUTPUT);
    digitalWrite(PIN_DEL_STATUS_1, HIGH);

    if (Server.begin() != 0)
    {
        digitalWrite(PIN_DEL_STATUS_2, HIGH);
        delay(500);
    }
}


void loop()
{
    OrderMgr orderManager;
    MotionControlSystem &motionControlSystem = MotionControlSystem::Instance();
    DirectionController &directionController = DirectionController::Instance();
    SlaveSensorLed &slaveSensorLed = SlaveSensorLed::Instance();
    SlaveActuator &slaveActuator = SlaveActuator::Instance();
    ContextualLightning contextualLightning;
    
    IntervalTimer motionControlTimer;
    motionControlTimer.priority(253);
    motionControlTimer.begin(motionControlInterrupt, PERIOD_ASSERV);

    uint32_t odometryReportTimer = 0;
    std::vector<uint8_t> odometryReport;
    std::vector<uint8_t> shortRangeSensorsValues;
    std::vector<uint8_t> longRangeSensorsValues;

    // Attente du démarrage de la grue
    digitalWrite(PIN_DEL_STATUS_2, HIGH);
    while (!slaveActuator.sensorDataAvailable())
    {
        slaveActuator.listen();
    }
    slaveActuator.getSensorsValues(longRangeSensorsValues);
    digitalWrite(PIN_DEL_STATUS_2, LOW);

    // Lancement de la carte capteurs
    slaveSensorLed.setLightningMode((uint8_t)SlaveSensorLed::ALL_OFF);

    // Attente du démarrage de la carte capteurs
    while (!slaveSensorLed.available())
    {
        slaveSensorLed.listen();
    }
    slaveSensorLed.getSensorsValues(shortRangeSensorsValues);

    // Affichage du succès du démarrage
    slaveSensorLed.setLightningMode((uint8_t)SlaveSensorLed::NIGHT_LIGHT_HIGH);

    uint32_t delTimer = 0;
    bool delState = true;

    while (true)
    {
        orderManager.execute();
        directionController.control();

        slaveActuator.listen();
        if (slaveActuator.sensorDataAvailable())
        {
            slaveActuator.getSensorsValues(longRangeSensorsValues);
        }

        slaveSensorLed.listen();
        if (slaveSensorLed.available())
        {
            slaveSensorLed.getSensorsValues(shortRangeSensorsValues);
        }

        contextualLightning.update();

        if (millis() - odometryReportTimer > ODOMETRY_REPORT_PERIOD)
        {
            odometryReportTimer = millis();

            odometryReport.clear();
            Position p = motionControlSystem.getPosition();
            Serializer::writeInt(p.x, odometryReport);
            Serializer::writeInt(p.y, odometryReport);
            Serializer::writeFloat(p.orientation, odometryReport);
            Serializer::writeFloat(motionControlSystem.getCurvature(), odometryReport);
            Serializer::writeUInt(motionControlSystem.getTrajectoryIndex(), odometryReport);
            Serializer::writeBool(motionControlSystem.isMovingForward(), odometryReport);
            odometryReport.insert(odometryReport.end(), shortRangeSensorsValues.begin(), shortRangeSensorsValues.end());
            odometryReport.insert(odometryReport.end(), longRangeSensorsValues.begin(), longRangeSensorsValues.end());
            Server.sendData(ODOMETRY_AND_SENSORS, odometryReport);

            motionControlSystem.sendLogs();
        }

        if (millis() - delTimer > 500)
        {
            delState = !delState;
            digitalWrite(PIN_DEL_STATUS_1, delState);
            delTimer = millis();
        }
    }
}


void motionControlInterrupt()
{
    static MotionControlSystem &motionControlSystem = MotionControlSystem::Instance();
    motionControlSystem.control();
}


/* Ce bout de code permet de compiler avec std::vector */
namespace std {
    void __throw_bad_alloc()
    {
        while (true)
        {
            Server.printf_err("Unable to allocate memory\n");
            delay(500);
        }
    }

    void __throw_length_error(char const*e)
    {
        while (true)
        {
            Server.printf_err(e);
            Server.println_err();
            delay(500);
        }
    }

    void __throw_out_of_range(char const*e)
    {
        while (true)
        {
            Server.printf_err(e);
            Server.println_err();
            delay(500);
        }
    }

    void __throw_out_of_range_fmt(char const*e, ...)
    {
        while (true)
        {
            Server.printf_err(e);
            Server.println_err();
            delay(500);
        }
    }
}

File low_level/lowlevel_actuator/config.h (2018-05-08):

#ifndef _CONFIG_h
#define _CONFIG_h

/* Report period */
#define REPORT_PERIOD   100  // ms

/* Master serial */
#define MASTER_SERIAL  Serial1
#define BAUDRATE_SERIAL 115200

/* Serial AX12 */
#define SERIAL_AX12             Serial2
#define SERIAL_AX12_BAUDRATE    1000000

/* Serial XL320 */
#define SERIAL_XL320            Serial3
#define SERIAL_XL320_BAUDRATE   1000000

#define ID_XL320_LEFT           1
#define ID_XL320_RIGHT          2


/* DELs */
#define PIN_DEL_GYRO_G  6
#define PIN_DEL_GYRO_D  20


/* Capteurs ToF */
#define PIN_EN_TOF_G    2
#define PIN_EN_TOF_D    13
#define PIN_EN_TOF_INT  14
#define PIN_EN_TOF_EXT  17


/* Moteurs */
#define PIN_EN_MOT_H    3
#define PIN_A_MOT_H     4
#define PIN_B_MOT_H     5
#define PIN_EN_MOT_V    21
#define PIN_A_MOT_V     22
#define PIN_B_MOT_V     23


/* Encodeurs */
#define PIN_ENC_MOT_H_A 11
#define PIN_ENC_MOT_H_B 12
#define PIN_ENC_MOT_V_A 15
#define PIN_ENC_MOT_V_B 16


/* Boutons */
#define PIN_BUTTON_GROUP_1  A10
#define PIN_BUTTON_GROUP_2  A11


/* Config bras */
#define FREQ_ASSERV		1000					// Fréquence d'asservissement (Hz)
#define PERIOD_ASSERV	(1000000 / FREQ_ASSERV)	// Période d'asservissement (µs)
#define AVERAGE_SPEED_SIZE  50
#define AX12_CONTROL_PERIOD 5  // ms

#define ID_AX12_HEAD    0
#define ID_AX12_PLIER   1

#define HMOTOR_TICK_TO_RAD  0.000865892 // radian/tick
#define VMOTOR_TICK_TO_MM   0.00489995  // mm/tick

#define BLOCKING_DELAY              600 // ms
#define BLOCKING_SENSIBILITY        0.05
#define BLOCKING_SPEED_THRESHOLD    0.4 // rad/s

#define H_SPEED_KP    900
#define H_SPEED_KI    15000
#define H_SPEED_KD    30

#define V_SPEED_KP    90
#define V_SPEED_KI    1500
#define V_SPEED_KD    3

#define HMOTOR_KP   10
#define HMOTOR_KD   0.5

#define HMOTOR_MAX_SPEED    3   // rad/s
#define HMOTOR_MIN_SPEED    0.3 // rad/s
#define VMOTOR_MAX_SPEED    30  // mm/s

#define ARM_MOVE_TIMEOUT    6000    // ms


#endif

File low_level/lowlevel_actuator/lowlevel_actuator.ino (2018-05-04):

#include "config.h"
#include "InternalCom.h"
#include "MotorSensor.h"
#include "ArmController.h"
#include "ArmPosition.h"
#include "Communication.h"
#include "SensorsMgr.h"
#include "UserInputControler.h"
#include "FlashingLights.h"
#include <Wire.h>


void setup()
{
}

void errorLoop()
{
    pinMode(PIN_DEL_GYRO_G, OUTPUT);
    pinMode(PIN_DEL_GYRO_D, OUTPUT);
    while (true)
    {
        for (int i = 0; i < 4; i++)
        {
            digitalWrite(PIN_DEL_GYRO_G, HIGH);
            digitalWrite(PIN_DEL_GYRO_D, HIGH);
            delay(100);
            digitalWrite(PIN_DEL_GYRO_G, LOW);
            digitalWrite(PIN_DEL_GYRO_D, LOW);
            delay(100);
        }
        delay(400);
    }
}

void loop()
{
    Serial.println("Coucou");
    pinMode(PIN_DEL_GYRO_G, OUTPUT);
    pinMode(PIN_DEL_GYRO_D, OUTPUT);
    digitalWrite(PIN_DEL_GYRO_G, HIGH);
    digitalWrite(PIN_DEL_GYRO_D, HIGH);
    Wire.begin();
    delay(500);

    Communication communication;
    SensorsMgr sensorsMgr;
    UserInputControler userInputControler;
    FlashingLights flashingLights(40, 800, 815);

    if (communication.init() != 0)
    {
        Serial.println("Communication init failed");
        errorLoop();
    }

    if (sensorsMgr.init() != 0)
    {
        Serial.println("Sensors init failed");
        errorLoop();
    }

    userInputControler.init();

    IntervalTimer timer;
    timer.priority(253);
    timer.begin(armControllerInterrupt, PERIOD_ASSERV);

    uint32_t reportTimer = 0;
    while (true)
    {
        communication.listenAndExecute();

        if (communication.newScoreAvailable())
        {
            userInputControler.setScore(communication.getScore());
        }

        if (communication.newSensorsAngle())
        {
            sensorsMgr.setAimAngles(communication.getLeftSensorAngle(), communication.getRightSensorAngle());
        }

        if (millis() - reportTimer > REPORT_PERIOD)
        {
            reportTimer = millis();
            int32_t tofG = 0, tofD = 0;
            float angleG = 0, angleD = 0;
            sensorsMgr.getSensorsData(tofG, tofD, angleG, angleD);
            communication.sendReport(tofG, tofD, angleG, angleD);
            //Serial.print("left=");
            //Serial.print(tofG);
            //Serial.print("  right=");
            //Serial.println(tofD);
        }

        sensorsMgr.updateServos();

        userInputControler.control();

        flashingLights.update();
    }
}

void armControllerInterrupt()
{
    static ArmController & armController = ArmController::Instance();
    armController.controlCCMotors();
}


/* Ce bout de code permet de compiler avec std::vector */
namespace std {
    void __throw_bad_alloc()
    {
        while (true)
        {
            Serial.printf("Unable to allocate memory\n");
            delay(500);
        }
    }

    void __throw_length_error(char const*e)
    {
        while (true)
        {
            Serial.println(e);
            delay(500);
        }
    }

    void __throw_out_of_range(char const*e)
    {
        while (true)
        {
            Serial.println(e);
            delay(500);
        }
    }

    void __throw_out_of_range_fmt(char const*e, ...)
    {
        while (true)
        {
            Serial.println(e);
            delay(500);
        }
    }
}

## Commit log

2017-08-07 Le code java du rover, avec des trucs en moins (le pathfinding, l'affichage, la config, …)
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2017-08-10 Renommage paquets et classes + buffer tampon pour les obstacles
2017-08-10 avancement de l'interface graphique de contrôle du LL
2017-08-12 Ajout d'infos. On sait ce que devient chaque mesure de capteurs et d'où viennent les obstacles.
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2017-08-14 Les tests utilisent un fichier de config à part
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2017-08-20 lowlevel interface : ajout fonctions de réception émission et traitement des données
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2017-09-15 Kraken a besoin des dimensions de la table
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2017-10-17 Utilisation de maven pour compiler simplement le projet
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2017-12-04 Ajout des obstacles fixes et des cubes
2018-01-04 Début de réflexions électroniques
    [camion-grue.brd, camion-grue.sch]
2018-01-04 Vieilles modifs de code, je sais plus trop ce que c'est... XD
2018-01-05 Ajout libs Eagle
    [camion-grue.brd, camion-grue.sch]
2018-01-05 maj elec et libs eagle
    [camion-grue.brd, camion-grue.sch]
2018-01-07 Elec: schéma presque ok + placement des composants
    [camion-grue.brd, camion-grue.sch]
2018-01-08 pin mapping teensy
    [camion-grue.brd, camion-grue.sch]
2018-01-08 Début de routage...
    [camion-grue.brd, camion-grue.sch]
2018-01-09 ajout carte elec grue
    [camion-grue.brd, camion-grue.sch, grue.brd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]
2018-01-10 Ajout lib Eagle DC-DC-converter
    [grue.brd, grue.sch]
2018-01-10 ajout doc pin mapping elec
    [Pin mapping.xlsx]
2018-01-10 Elec: routage catre principale presque fini !
    [camion-grue.brd, camion-grue.sch]
2018-01-11 Elec cockpit terminée
    [camion-grue.brd, camion-grue.sch]
2018-01-12 Carte secondaire : schéma presque fini, il manque juste 2 pins à la teensy... :'(
    [grue.brd, grue.sch]
2018-01-12 Comment ça il n'y a plus de pins dispo ? mais enfin tout va bien !
    [grue.brd, grue.sch]
2018-01-13 L'élec ça c'est fait !
    [grue.brd, grue.sch]
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2018-01-16 Utilise une PriorityBlockingQueue pour les messages de communication sortants
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2018-01-16 Stream trop long à être éteint : une durée max plutôt qu'un nombre de message
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2018-01-19 Elec: ajout doc
    [camion-grue.brd]
2018-01-19 Elec balise: un bon début :)
    [balise.brd, balise.sch]
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2018-01-20 Ajout OrderMgr pour faire des pings pour de vrai ! Et plus si affinités...
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2018-01-21 Bugfix du bugfix…
2018-01-22 maj elec balise
    [balise.brd, balise.sch]
2018-01-22 Elec: Ajout refs RS
    [camion-grue.brd, camion-grue.sch]
2018-01-22 LL: bugfix message d'erreur intempestif
    [CommunicationServer.cpp]
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2018-02-03 Ajout élec balise
    [balise.brd, balise.sch]
2018-02-03 Elec balise routée !
    [balise.brd, balise.sch]
2018-02-03 Elec robot: régulateur 5V dédié pour la logique, indépendant de celui de la RPI
    [camion-grue.brd, camion-grue.sch]
2018-02-04 Elec version finale + Ajout fichiers gerber
    [balise.brd, balise.sch, grue.brd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]
2018-02-04 Elec: début de liste de courses
    [BOM-camion-grue-complet.csv, intech-senpai-camion-grue-complet.brd]
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2018-02-13 Bugfix check deconnexion LL
    [CommunicationServer.cpp]
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2018-02-16 Revert "Sauvegarde du code LL avant de tout casser"
    This reverts commit 21cdad873b082bdfab5906957f14ebadb3b6825d.
    [CommunicationServer.cpp]
2018-02-16 Déco / reco opérationnel (en utilisant la lib corrigée)
    [CommunicationServer.cpp]
2018-03-08 définition de l'architecture du bas niveau + code de base avec communication et locomotion
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2018-03-17 Détails des ordres du protocole de comm
    [Protocole-ordres.ods]
2018-03-17 Mise à jour protocole
    [Protocole-ordres.ods]
2018-03-17 Quelques ajustements des ordres
    [Protocole-ordres.ods]
2018-03-17 Le traitement des données de comm utilise maintenant un ByteBuffer. Ça permet de simplifier la lecture d'int, de float, etc.
2018-03-17 int32 à la place de uint32 dans le protocole
    [Protocole-ordres.ods]
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2018-03-20 MAJ protocole-ordres
    [Protocole-ordres.ods]
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2018-03-20 Doc protocole: simplification des commandes de débug
    [Protocole-ordres.ods]
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2018-04-01 Affichage + bugfix forme robot + script création de chemin
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2018-04-02 maj format des données capteurs
    [Protocole-ordres.ods]
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2018-04-02 Lowlevel cleanup and better logs
    [Protocole-ordres.ods]
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2018-04-04 Correction du calcul des positions et angles des tourelles
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2018-04-06 Small bugfix. Odometry and sensors stream functional
    [SensorsMgr.h, lowlevel_master.ino, lowlevel_sensor.ino]
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2018-04-11 Modification protocole
    [Protocole-ordres.ods]
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2018-04-16 bugfix + asserv grue
    [ArmController.h, ArmPosition.h, config.h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]
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2018-04-19 On vérifie quand même les collisions en mode dégradé…
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2018-04-19 Fix utilisation de chemins connus
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2018-04-22 Small bugfix + ajout ordres LL
    [ArmController.h, ArmPosition.h, SmartArmController.h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]
2018-04-25 Affichage du score sur 7 segments + contrôle manuel des mouvements de la tourelle
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2018-04-29 Mise a jour doc protocole
    [Protocole-ordres.ods]
2018-04-29 Ajout code retour actionneur TIMEOUT
    [Protocole-ordres.ods]
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2018-04-30 LL: implem waitForJumper + bugfix scripts bras
    [ArmPosition.h, SmartArmController.h]
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2018-05-02 On spamme plus de STOP le LL + buffer capteur plus petit
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2018-05-02 LL: arrêt d'urgence beaucoup plus rapide + logs de distance de freinage
2018-05-03 Désactivation d'obstacles pour test + désactivation de la replannification pour le moment
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2018-05-03 Support XL320 tourelle + ToF longue portée + augmentation de portée des ToF courte portée
2018-05-03 Update protocole + visée tourelles HL
    [Protocole-ordres.ods]
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2018-05-04 Bugfix collision de détection
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2018-05-05 On désactive le thread de commande de tourelles si elles sont désactivées
2018-05-05 Capteurs tourelle: renvoient DEAD lorsque la tourelle tourne; Ajout de Logs Série sur la Teensy DELs&capteurs pour visualiser les données ToF courte portée
2018-05-05 Bugfix détection de collision
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2018-05-05 LL actuator: add debug LEDs for mysterious bug tracking
    [SensorsMgr.h, lowlevel_actuator.ino]
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2018-05-05 La distance au script de prise de cube dépend aussi de l'orientation
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2018-05-06 Script domotique v2
    [Protocole-ordres.ods]
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2018-05-07 LL arm: XL320 debug checksum calc + update error handling
    [SensorsMgr.h, lowlevel_actuator.ino]
2018-05-07 bugfix saturation liaison I2C bras
    [Communication.h, SensorsMgr.h, config.h]
2018-05-07 bugfix error handling qui bloquait tout lol
    [ArmController.h, SmartArmController.h]
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2018-05-08 MAJ ordres bras + peaufinage des scripts LL associés
    [Protocole-ordres.ods]
2018-05-08 LL fix script takeCube qui pouvait dégager celui stocké
    [SmartArmController.h]
2018-05-08 LL bufix des scripts pour ne pas défoncer notre belle pile de cubes :)
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2018-05-09 correction détection blocage de l'ax 12 de tête
    [ArmController.h, SmartArmController.h]
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2018-05-09 Si le robot a déjà un cube, il n'en prendra pas un autre s'il lui reste moins de 20s
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
